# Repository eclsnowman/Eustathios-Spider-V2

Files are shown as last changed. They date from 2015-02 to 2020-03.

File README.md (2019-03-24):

# Eustathios Spider - V2
Update to Eustathios with a little bit of HercuLien design changes.

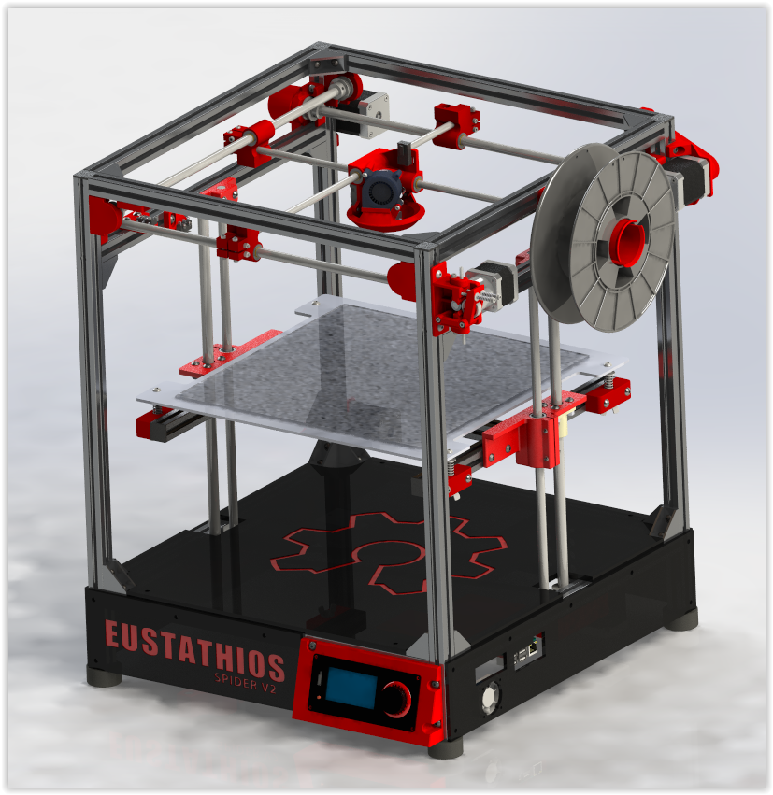
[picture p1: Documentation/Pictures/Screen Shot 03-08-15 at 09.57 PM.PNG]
Eustathios Spider - V2 Render Image


Hello and welcome to my github for Eustathios Spider V2 3D printer. This printer is my attempt to make additional modifications and improvements to the original Eustathios Spider design I published earlier. This has been no small task since the Eustathios printer (designed by Jason Smith) was such an exceptional design to begin with. Now that Google+ has died, the Community around the HercuLien printer and the Eustathios printer have moved to: https://forum.makerforums.info/c/herculien . This is thanks in great part to Michael K Johnson, who worked his magic to retain the years of great community interaction on G+ and ported it into the Discourse community over on Makerforums. If you are looking for support or community interaction on these printers moving forward, this is the place to go.

This family of printers is all based on the X/Y gantry mechanics of the Ultimaker. Ultimaker style mechanics utilizes a light hot-end/carriage which gets constrained by one X and one Y cross rod. Connected to these cross rods are rod ends which ride on side shafts that act both for power transmission of one axis (rotation) and as the linear guide for travel of the other axis (translation).

 Originally a gentlemen who goes by the name Sublime (https://github.com/Intrinsically-Sublime/Tantillus/) created a small format variant of the Ultimaker mechanics which he called the Tantillus. Then GoopyPlastic (aka Brad Hill) created an extrusion version of the Tantillus called the tslot Tantillus (https://github.com/goopyplastic/tslot-tantillus). Following in Brad’s footsteps Tim Rastall (https://plus.google.com/u/0/+TimRastall/posts) created the very popular Ingentis printer (https://www.youmagine.com/designs/ingentis-a-tantillus-variant) which is a larger version of Tantilus using thicker linear guide components, spectra drive system, and a much larger build envelope. The next printer in this design family was by Jason Smith (https://plus.google.com/u/0/103009815307828556107/posts) call the Eustathios (https://github.com/jasonsmit4/Eustathios). This is the printer that got me excited about this family of printers. Jason made several design choices like GT2 belts which I felt were great upgrades to the platform. I lucked out because his release was timed perfectly with a promotion Misumi was running where your first order from them up to $150 in value was free. I wanted to be able to modify Jason’s files slightly, but he had modeled everything in Sketchup. My limited experience was with Solidworks (self taught) so rather than learn new software I redrew Jason’s Eustathios design files from scratch. And so my Eustathios Spider V1 variant , named due to the color scheme, was born (https://github.com/eclsnowman/Lien3D_Eustathios_Spider). I built the Eustathios and fell in love with the smooth operation, clean prints, and overall reliability. So after operating the Eustathios for several months I converted my existing large CoreXY Printer (https://github.com/eclsnowman/Lien3D_CoreXY ) into a X/Y gantry printer with larger cross rods and dual extrusion. The name of this printer is HercuLien (https://github.com/eclsnowman/HercuLien).

Sorry for the long history lesson, but as you can see there is a lot of progress and talented people involved in these projects. Also I wanted to make sure credit is properly attributed to the many great makers who have come before me. The caliber of people involved and all the creativity in the platform is what keeps me so motivated.

Eustathios Spider V2 Overview:

Build Volume: 285x285x295mm

Controler: Azteeg X5 Mini with Viki2 LCD display

Single Extruder, 200W 24V power supply for controls, 120V 500W heated bed through SSR control.

Documentation:

BOM = https://github.com/eclsnowman/Eustathios-Spider-V2/blob/master/Documentation/BOM/Eustathios%20Spider%20V2%20BOM.xlsx

Printable STL Parts = https://github.com/eclsnowman/Eustathios-Spider-V2/tree/master/STL%20Print%20FIles

Solidworks Files = https://github.com/eclsnowman/Eustathios-Spider-V2/tree/master/STL%20Print%20FIles

Other 3D model formats in 7zip due to github 50mb limit) = https://github.com/eclsnowman/Eustathios-Spider-V2/tree/master/Other%203D%20Formats

3D renders: https://github.com/eclsnowman/Eustathios-Spider-V2/tree/master/Documentation/Pictures

Image of printed parts:
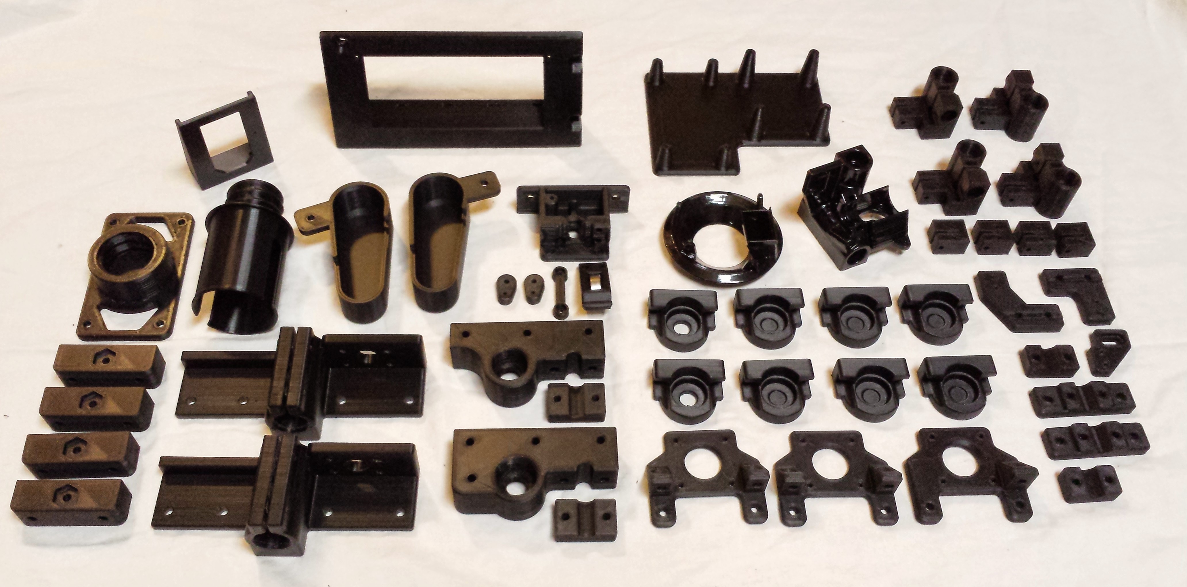
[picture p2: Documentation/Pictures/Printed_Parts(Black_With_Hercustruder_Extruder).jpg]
Eustathios Spider - V2 Printed Parts Image


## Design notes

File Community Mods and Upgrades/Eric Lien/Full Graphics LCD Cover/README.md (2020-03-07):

Note this works for the V1.5 Frame, but not yet for the V2 frame due to the lower frame crossbars. I am working on updating it for the V2 frame.

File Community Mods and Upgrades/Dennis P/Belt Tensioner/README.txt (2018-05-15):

Remix of Walter Hsiao's 8mm Belt tensioner. Changes include bores for brass thread heatserts for the M5 and M3 screws. 

Left and Right delimiter is arbitrary- its only used to describe the 2 mirror images. 

Required fasteners are: 
M5x25 for the 8mm rod clamp 
M3x30 for the belt tensioner

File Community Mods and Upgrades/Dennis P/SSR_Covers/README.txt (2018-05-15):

The knockoff uxcell SSR-10DA 10A DC 3-32V to AC 24V-380V SSR Solid State I used did not have terminal protectors on either the high or low voltage terminals. 

These covers were designed for M4 fixing screws to be utilized with hammer nuts in your extrusion or to the provided heatsink.

The 3mm LED hole is for a pre-wired 12V indicator LED to be used on the 12V side, wired in parallel to the heatbed trigger circuit so that you may be able to visually verify that the SSR is being triggered by the controller board.

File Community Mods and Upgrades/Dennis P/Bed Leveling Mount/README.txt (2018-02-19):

Bed Levelling Mount Remix by D. Pantazis

1. Bed levelling blocks reconfigured with annotations for adjusting the nozzle / bed gap. 

2. Graduated thumb wheel to aid in adjusting the bed. 

3. Test flat of the recessed test to tweak printer settings. 

4. Spring keeper centering washer for top of spring. To center and align the spring to the M5 stud/nut. 

Blocks attach to 20x20 frame with M5x20 cap head screws. 

Levelling studs for bed attachment M5x60 double nutted to heat spreader plate.  

Springs are 1/2" OD x 1" min length.

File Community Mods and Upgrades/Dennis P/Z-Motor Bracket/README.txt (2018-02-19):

Alternate Z motor mount bracket- I goofed when I ordered belts and ordered one too short.
 
I decided to make use of an additional crossbar and put the tensioner on a revised Z motor mount. 

Z Motor rotated 45 degrees to get the tensioner closer to the spindle to get better belt wrap on the idler and motor pulley.

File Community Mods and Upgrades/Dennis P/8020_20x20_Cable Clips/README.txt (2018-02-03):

8020 profiles are a little different than some of the other ones, notably the channel is 5.25mm wide. 

These cable clips are designed to twist in through the slots. 

If you print with a brim, leave the brim on the toggle and stud, it will act as a spring to keep the clip snugly in place.

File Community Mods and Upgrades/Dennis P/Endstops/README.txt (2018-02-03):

Makerbot style endstop switch holders for X, Y & Z axis. 

Included are holders for both MAX & MIN locations, though only the MIN's are normally required. 

Reliefs in the parts for the solder buildup and header pins may required some adjustment and opening up for the PCB's to sit flat. YMMV....

The thru fixing holes in brackets are 2.5mm for making threads with an M3 spiral point tap so that the chips eject out the back of the part.

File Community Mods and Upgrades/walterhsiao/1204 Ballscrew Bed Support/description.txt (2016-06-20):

Replacement for Z_Axis_Bed_Support, designed to be compatible to 1204 ballscrews instead of the 12mm lead screws.  More info at http://www.thingiverse.com/thing:854267

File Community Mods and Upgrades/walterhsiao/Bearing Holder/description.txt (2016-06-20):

Alternate bearing holder design.  More info at http://www.thingiverse.com/thing:854360

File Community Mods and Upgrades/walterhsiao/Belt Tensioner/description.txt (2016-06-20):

Alternate belt tensioner design, designed to be used with graphite bushings and supports slightly longer cross rods.  Versions are available for 8mm and 10mm cross rods.  More info at http://www.thingiverse.com/thing:854301

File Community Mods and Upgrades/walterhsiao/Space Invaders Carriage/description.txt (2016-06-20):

Alternate E3Dv6 carriage design.  Nozzle height is significantly higher than the original carriage and my not be compatible without other changes.  More info at http://www.thingiverse.com/thing:1322641.

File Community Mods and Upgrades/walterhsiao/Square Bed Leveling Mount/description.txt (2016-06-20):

Replacement for Bed_Leveling_Mount, designed to be used with a rectangular heated bed.  More info at http://www.thingiverse.com/thing:854260

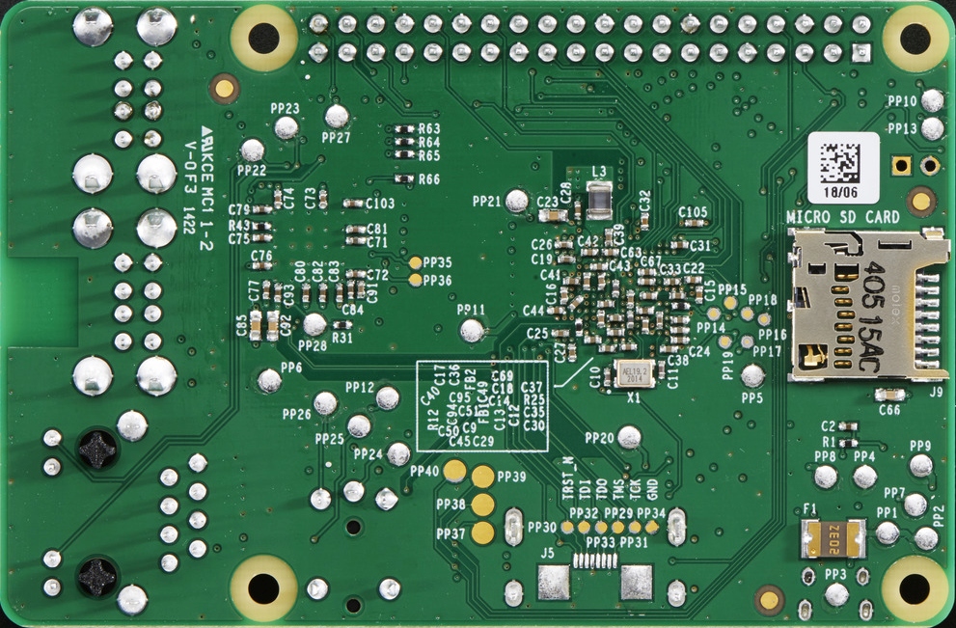
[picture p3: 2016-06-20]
Solidworks/Electronics/Amazon/Raspberry Pi/@raspberry_pi_model_B+_bot_2.jpg

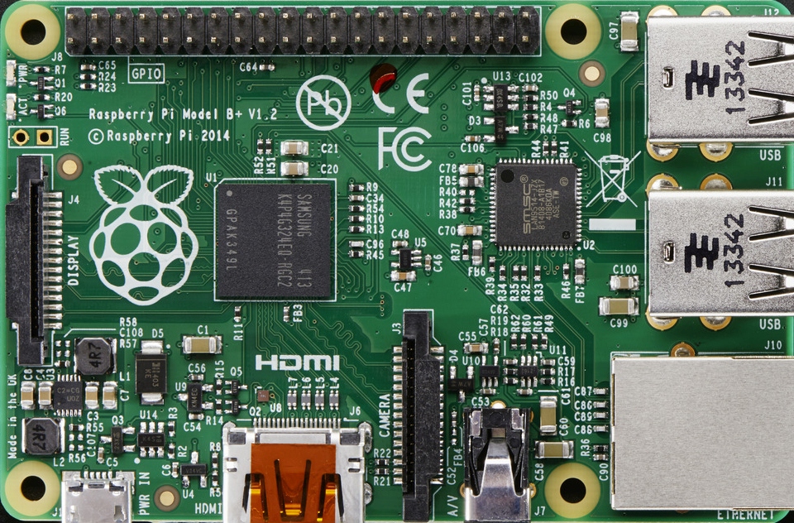
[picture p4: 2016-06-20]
Solidworks/Electronics/Amazon/Raspberry Pi/@raspberry_pi_model_B+_top_1.jpg

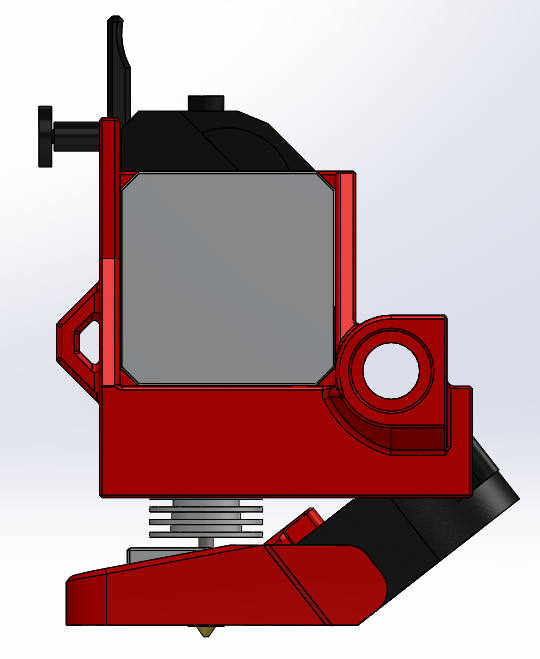
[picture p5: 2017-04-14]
Community Mods and Upgrades/Eric Lien/Eustathios BMG Carriage/Pictures/Screen Shot 04-14-17 at 12.22 PM 002.PNG

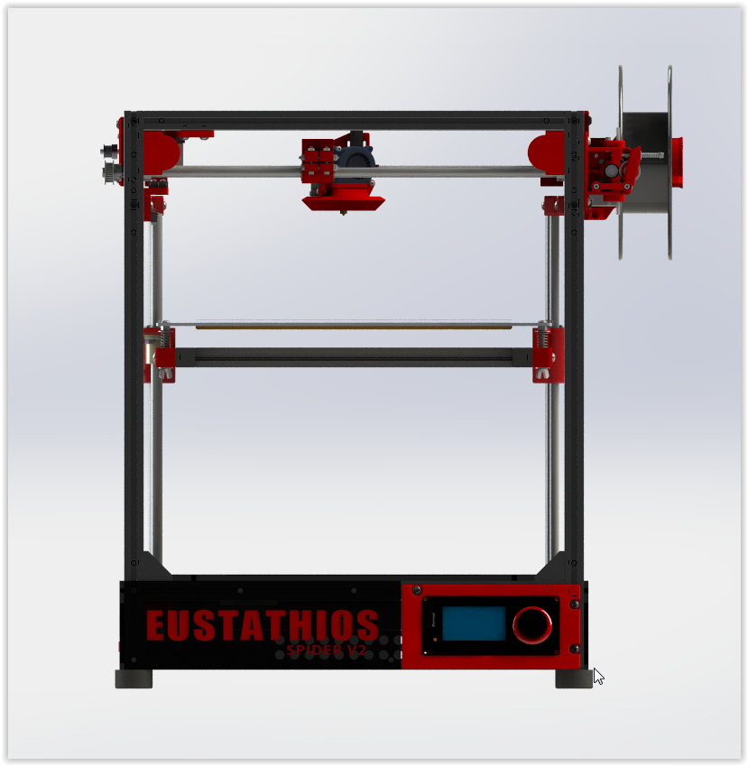
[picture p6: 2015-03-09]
Documentation/Pictures/Screen Shot 03-08-15 at 04.17 PM.PNG

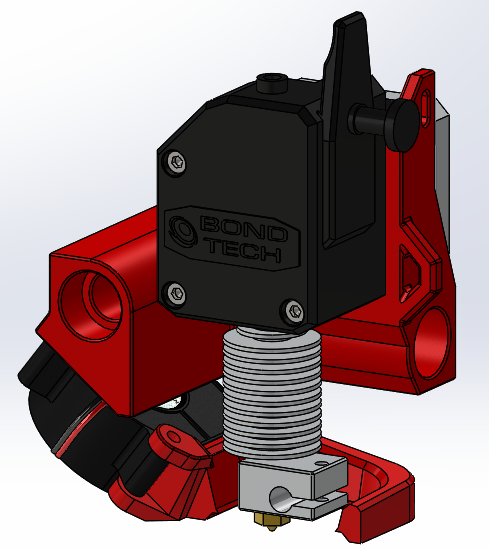
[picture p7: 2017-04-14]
Community Mods and Upgrades/Eric Lien/Eustathios BMG Carriage/Pictures/Screen Shot 04-14-17 at 12.23 PM.PNG

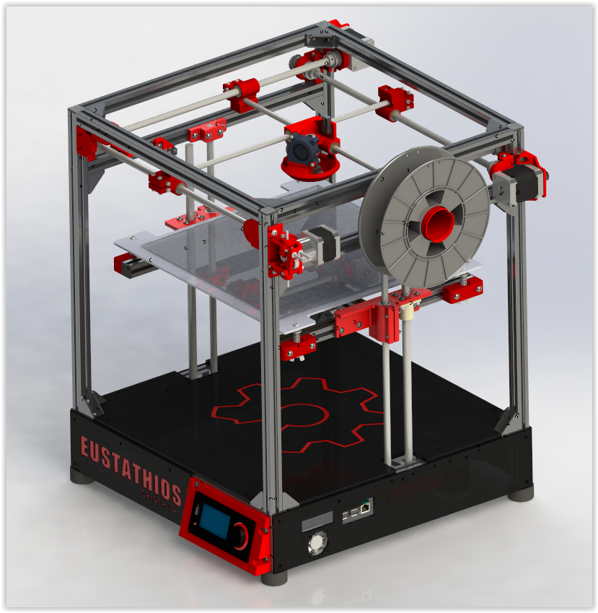
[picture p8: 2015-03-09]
Documentation/Pictures/Screen Shot 03-08-15 at 04.13 PM.PNG

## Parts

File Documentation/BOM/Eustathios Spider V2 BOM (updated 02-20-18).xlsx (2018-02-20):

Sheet: SUBASSY
SUBASSY # | ITEM NO. | PART NUMBER | DESCRIPTION | Vendor | Qty of SUBASSY | Qty per SUBASSY | Total Per SUBASSY
1 |  | Eustathios_Frame |  |  | 1
 | 1.1 | HFSB5-2020-562-LTP-RCP-FR-AH470-AP80 | 20x20x562mm Extruded Aluminum W/ Holes | Misumi or SMW3D |  | 4 | 4
 | 1.2 | HFSB5-2020-425-TPW | 20x20x425mm Extruded Aluminum W/ Tapped Ends | Misumi or SMW3D |  | 10 | 10
 | 1.3 | 91239A224 | 5mm x 10mm button head screw (100 Pack) | McMaster |  | 20 | 20
 | 1.4 | HFC5-2020-B | Black Extrusion Endcap | Misumi |  | 4 | 4
 | 1.5 | HBLFSNB5_W_Hardware | Corner Bracket Subassy | NA (Subassembly) | 16
 | 1.5.1 | HBLFSNB5 | 5 Series, Reversal Brackets with Tab | Misumi |  | 1 | 16
 | 1.5.2 | HNTTSN5-5 | T-Slot Nuts | Misumi or SMW3D |  | 2 | 32
 | 1.5.3 | 91239A224 | 5mm x 10mm button head screw | McMaster |  | 2 | 32
 | 1.6 | 9540K28 | 1.5inX.75inX.25inHole_Foot (10 Pack) | McMaster |  | 4 | 4
 | 1.7 | 91239A232 | 5mm x 16mm button head socket cap screw | McMaster |  | 4 | 4
 | 1.8 | Jamicon_KF0410-01 | 40x40mm 24v fan | Ultimachine |  | 1 | 1
 | 1.9 | Acrylic_or_Polycarbonate_Bottom_Plate | Fabricated - .177in thick Acrylic or Polycarbonate | Amazon |  | 1 | 1
 | 1.10 | Acrylic_or_Polycarbonate_Right_Bottom | Fabricated - .177in thick Acrylic or Polycarbonate | Amazon |  | 1 | 1
 | 1.11 | Acrylic_or_Polycarbonate_Back_Bottom | Fabricated - .177in thick Acrylic or Polycarbonate | Amazon |  | 1 | 1
 | 1.12 | Acrylic_or_Polycarbonate_Left_Bottom | Fabricated - .177in thick Acrylic or Polycarbonate | Amazon |  | 1 | 1
 | 1.13 | Acrylic_or_Polycarbonate_Front_Bottom | Fabricated - .177in thick Acrylic or Polycarbonate | Amazon |  | 1 | 1
2 |  | XY_Axis_A |  |  | 1
 | 2.1 | SFJ10-458 | 10mm OD x 458mm Long Precision Linear Shaft | Misumi or SMW3D |  | 1 | 1
 | 2.2 | 10mm_Rod_End_Bearing_Assembly | End Bearing Subassy | NA (Subassembly) | 2
 | 2.2.1 | Bearing_Holder | 3D Printed | 3D Printed |  | 1 | 2
 | 2.2.2 | 5972K164 | 10mm x 22mm x 6mm (6900 series bearing) | Robotdigg |  | 1 | 2
 | 2.2.3 | 92095A210 | 5mm x 12mm button head socket cap screw | McMaster |  | 2 | 4
 | 2.2.4 | HNTTSN5-5 | T-Slot Nuts | Misumi or SMW3D |  | 2 | 4
 | 2.2.5 | GT2_Aluminum_Timing_Pulley_32_Tooth | GT2 2mm pitch, 10mm ID, 32 tooth pulley | Robotdigg |  | 1 | 2
 | 2.2.6 | 90214A422 | 10mmx16mmx0.5mm_SHim | McMaster |  | 1 | 2
 | 2.3 | XY_Axis_Belt_Tensioner_A | Rod End With Tensioner (Type A) Subassy | NA (Subassembly) | 1
 | 2.3.1 | XY Axis Belt Tensioner A | 3D Printed | 3D Printed |  | 1 | 1
 | 2.3.2 | a_7z41mpsb10m | 10mm self aligning bronze sintered bushings | Ultibots or SDP/SI or Spyraflo or McMaster |  | 2 | 2
 | 2.3.3 | XY Axis Belt Tensioner End | 3D Printed | 3D Printed |  | 1 | 1
 | 2.3.4 | 91290A125 | 3mm x 25mm socket head cap screw | McMaster |  | 2 | 2
 | 2.3.5 | 90591A121 | 3mm hex nut (Din 934) | McMaster |  | 2 | 2
 | 2.3.6 | 91239A232 | 5mm x 16mm button head socket cap screw | McMaster |  | 1 | 1
 | 2.3.7 | 90591A146 | 3mm standard hex nut (DIN 934) | McMaster |  | 1 | 1
 | 2.3.8 | 90576A102 | 3mm nylock hex nut | McMaster |  | 2 | 2
 | 2.3.9 | 91290A135 | 3mm x 35mm socket head cap screw | McMaster |  | 2 | 2
3 |  | XY_Axis_A (Driven Version/Configuration) |  |  | 1
 | 3.1 | 10mm_Rod_End_Bearing_Assembly (Passthrough) | End Bearing Subassy (Passthrough) | NA (Subassembly) | 1
 | 3.1.1 | Passthrough_Bearing_Holder | 3D Printed | 3D Printed |  | 1 | 1
 | 3.1.2 | 5972K164 | 10mm x 22mm x 6mm (6900 series bearing) | Fasteddy Bearings |  | 1 | 1
 | 3.1.3 | 92095A210 | 5mm x 12mm button head socket cap screw | McMaster |  | 2 | 2
 | 3.1.4 | HNTTSN5-5 | T-Slot Nuts | Misumi or SMW3D |  | 2 | 2
 | 3.1.5 | GT2_Aluminum_Timing_Pulley_32_Tooth | GT2 2mm pitch, 10mm ID, 32 tooth pulley | Robotdigg |  | 1 | 1
 | 3.1.6 | 90214A422 | 10mmx16mmx0.5mm_SHim | McMaster |  | 1 | 1
 | 3.2 | 10mm_Rod_End_Bearing_Assembly | End Bearing Subassy | NA (Subassembly) | 1
 | 3.2.1 | Bearing_Holder | 3D Printed | 3D Printed |  | 1 | 1
 | 3.2.2 | 5972K164 | 10mm x 22mm x 6mm (6900 series bearing) | Fasteddy Bearings |  | 1 | 1
 | 3.2.3 | 92095A210 | 5mm x 12mm button head socket cap screw | McMaster |  | 2 | 2
 | 3.2.4 | HNTTSN5-5 | T-Slot Nuts | Misumi or SMW3D |  | 2 | 2
 | 3.2.5 | GT2_Aluminum_Timing_Pulley_32_Tooth | GT2 2mm pitch, 10mm ID, 32 tooth pulley | Robotdigg |  | 1 | 1
 | 3.2.6 | 90214A422 | 10mmx16mmx0.5mm_SHim | McMaster |  | 1 | 1
 | 3.3 | XY_Axis_Belt_Tensioner_A | Rod End With Tensioner (Type A) Subassy | NA (Subassembly) | 1
 | 3.3.1 | XY Axis Belt Tensioner A | 3D Printed | 3D Printed |  | 1 | 1
 | 3.3.2 | a_7z41mpsb10m | 10mm self aligning bronze sintered bushings | Ultibots or SDP/SI or Spyraflo or McMaster |  | 2 | 2
 | 3.3.3 | XY Axis Belt Tensioner End | 3D Printed | 3D Printed |  | 1 | 1
 | 3.3.4 | 91290A125 | 3mm x 25mm socket head cap screw | McMaster |  | 2 | 2
 | 3.3.5 | 90591A121 | 3mm hex nut (Din 934) | McMaster |  | 2 | 2
 | 3.3.6 | 91239A232 | 5mm x 16mm button head socket cap screw | McMaster |  | 1 | 1
 | 3.3.7 | 90591A146 | 3mm standard hex nut (DIN 934) | McMaster |  | 1 | 1
 | 3.3.8 | 90576A102 | 3mm nylock hex nut | McMaster |  | 2 | 2
 | 3.3.9 | 91290A135 | 3mm x 35mm socket head cap screw | McMaster |  | 2 | 2
 | 3.4 | SFJ10-483 | 10mm OD x 483mm Long Precision Linear Shaft | Misumi or SMW3D |  | 1 | 1
 | 3.5 | GT2_Aluminum_Timing_Pulley_32_Tooth | GT2 2mm pitch, 10mm ID, 32 tooth pulley | Robotdigg |  | 1 | 1
4 |  | XY_Axis_B |  |  | 1
 | 4.1 | SFJ10-458 | 10mm OD x 458mm Long Precision Linear Shaft | Misumi or SMW3D |  | 1 | 1
 | 4.2 | 10mm_Rod_End_Bearing_Assembly | End Bearing Subassy | NA (Subassembly) | 2
 | 4.2.1 | Bearing_Holder | 3D Printed | 3D Printed |  | 1 | 2
 | 4.2.2 | 5972K164 | 10mm x 22mm x 6mm (6900 series bearing) | Fasteddy Bearings |  | 1 | 2
 | 4.2.3 | 92095A210 | 5mm x 12mm button head socket cap screw | McMaster |  | 2 | 4
 | 4.2.4 | HNTTSN5-5 | T-Slot Nuts | Misumi or SMW3D |  | 2 | 4
 | 4.2.5 | GT2_Aluminum_Timing_Pulley_32_Tooth | GT2 2mm pitch, 10mm ID, 32 tooth pulley | Robotdigg |  | 1 | 2
 | 4.2.6 | 90214A422 | 10mmx16mmx0.5mm_SHim | McMaster |  | 1 | 2
 | 4.3 | XY_Axis_Belt_Tensioner_B | Rod End With Tensioner (Type B) Subassy | NA (Subassembly) | 1
 | 4.3.1 | XY Axis Belt Tensioner B | 3D Printed | 3D Printed |  | 1 | 1
 | 4.3.2 | a_7z41mpsb10m | 10mm self aligning bronze sintered bushings | Ultibots or SDP/SI or Spyraflo or McMaster |  | 2 | 2
 | 4.3.3 | XY Axis Belt Tensioner End | 3D Printed | 3D Printed |  | 1 | 1
 | 4.3.4 | 91290A135 | 3mm x 35mm socket head cap screw | McMaster |  | 2 | 2
 | 4.3.5 | 90576A102 | 3mm nylock hex nut | McMaster |  | 4 | 4
 | 4.3.6 | 91239A126 | 3mm x 25mm button head socket cap screw | McMaster |  | 2 | 2
 | 4.3.7 | 90591A146 | 3mm standard hex nut (DIN 934) | McMaster |  | 1 | 1
 | 4.3.8 | 91239A232 | 5mm x 16mm button head socket cap screw | McMaster |  | 1 | 1
5 |  | XY_Axis_B (Driven Version/Configuration) |  |  | 1
 | 5.1 | 10mm_Rod_End_Bearing_Assembly (Passthrough) | End Bearing Subassy (Passthrough) | NA (Subassembly) | 1
 | 5.1.1 | Passthrough_Bearing_Holder | 3D Printed | 3D Printed |  | 1 | 1
 | 5.1.2 | 5972K164 | 10mm x 22mm x 6mm (6900 series bearing) | Fasteddy Bearings |  | 1 | 1
 | 5.1.3 | 92095A210 | 5mm x 12mm button head socket cap screw | McMaster |  | 2 | 2
 | 5.1.4 | HNTTSN5-5 | T-Slot Nuts | Misumi or SMW3D |  | 2 | 2
 | 5.1.5 | GT2_Aluminum_Timing_Pulley_32_Tooth | GT2 2mm pitch, 10mm ID, 32 tooth pulley | Robotdigg |  | 1 | 1
 | 5.1.6 | 90214A422 | 10mmx16mmx0.5mm_SHim | McMaster |  | 1 | 1
 | 5.2 | 10mm_Rod_End_Bearing_Assembly | End Bearing Subassy | NA (Subassembly) | 1
 | 5.2.1 | Bearing_Holder | 3D Printed | 3D Printed |  | 1 | 1
 | 5.2.2 | 5972K164 | 10mm x 22mm x 6mm (6900 series bearing) | Fasteddy Bearings |  | 1 | 1
 | 5.2.3 | 92095A210 | 5mm x 12mm button head socket cap screw | McMaster |  | 2 | 2
 | 5.2.4 | HNTTSN5-5 | T-Slot Nuts | Misumi or SMW3D |  | 2 | 2
 | 5.2.5 | GT2_Aluminum_Timing_Pulley_32_Tooth | GT2 2mm pitch, 10mm ID, 32 tooth pulley | Robotdigg |  | 1 | 1
 | 5.2.6 | 90214A422 | 10mmx16mmx0.5mm_SHim | McMaster |  | 1 | 1
 | 5.3 | XY_Axis_Belt_Tensioner_B | Rod End With Tensioner (Type B) Subassy | NA (Subassembly) | 1
 | 5.3.1 | XY Axis Belt Tensioner B | 3D Printed | 3D Printed |  | 1 | 1
 | 5.3.2 | a_7z41mpsb10m | 10mm self aligning bronze sintered bushings | Ultibots or SDP/SI or Spyraflo or McMaster |  | 2 | 2
 | 5.3.3 | XY Axis Belt Tensioner End | 3D Printed | 3D Printed |  | 1 | 1
 | 5.3.4 | 91290A135 | 3mm x 35mm socket head cap screw | McMaster |  | 2 | 2
 | 5.3.5 | 90576A102 | 3mm nylock hex nut | McMaster |  | 4 | 4
 | 5.3.6 | 91239A126 | 3mm x 25mm button head socket cap screw | McMaster |  | 2 | 2
 | 5.3.7 | 90591A146 | 3mm standard hex nut (DIN 934) | McMaster |  | 1 | 1
 | 5.3.8 | 91239A232 | 5mm x 16mm button head socket cap screw | McMaster |  | 1 | 1
 | 5.4 | SFJ10-483 | 10mm OD x 483mm Long Precision Linear Shaft | Misumi or SMW3D |  | 1 | 1
 | 5.5 | GT2_Aluminum_Timing_Pulley_32_Tooth | GT2 2mm pitch, 10mm ID, 32 tooth pulley | Robotdigg |  | 1 | 1
6 |  | Y_Axis_Endstop |  |  | 1
 | 6.1 | Y Endstop Mount | 3D Printed | 3D Printed |  | 1 | 1
 | 6.2 | Micro Switch Button | NO / NC Limit Switch | Robotdigg or SMW3D |  | 1 | 1
 | 6.3 | HNTTSN5-5 | T-Slot Nuts | Misumi or SMW3D |  | 2 | 2
 | 6.4 | 92095A210 | 5mm x 12mm button head socket cap screw | McMaster |  | 2 | 2
 | 6.5 | 92095A183 | 3mm x 12mm button head socket cap screw | McMaster |  | 2 | 2
7 |  | X_Axis_Endstop |  |  | 1
 | 7.1 | X Endstop Mount | 3D Printed | 3D Printed |  | 1 | 1
 | 7.2 | Micro Switch Button | NO / NC Limit Switch | Robotdigg or SMW3D |  | 1 | 1
 | 7.3 | HNTTSN5-5 | T-Slot Nuts | Misumi or SMW3D |  | 2 | 2
 | 7.4 | 92095A210 | 5mm x 12mm button head socket cap screw | McMaster |  | 2 | 2
 | 7.5 | 92095A183 | 3mm x 12mm button head socket cap screw | McMaster |  | 2 | 2
8 | 8.1 | SFJ8-400 | 8mm OD x 400mm Long Precision Linear Shaft | Misumi or SMW3D |  |  | 2
9 |  | Eustathios_Carriage_V4_Molex_Microfit_3 |  |  | 1
 | 9.1 | Carriage_V4_Molex_Microfit_3 | 3D Printed | 3D Printed |  | 1 | 1
 | 9.2 | 4020Blower | 4020 part cooling blower fan | Ebay |  | 1 | 1
 | 9.3 | E3D_V6 | Hot End (need 24V fan and heater cartridge if 24V power supply is used, by default E3D V6 is designed for 12V system) | E3D or SMW3D |  | 1 | 1
 | 9.4 | 30x30_Fan | included with e3d kit (needs to be 24v if 24V power supply is used) | See Above |  | 1 | 1
 | 9.5 | Carriage_V4_Part_Cooling_Duct | 3D Printed | 3D Printed |  | 1 | 1
 | 9.6 | a_7z41mpsb08m | 8mm self aligning bronze sintered bushings | Ultibots or SDP/SI or Spyraflo or McMaster |  | 4 | 4
 | 9.7 | Molex_430200801 | Molex 430200801 Subassy | NA (Subassembly) | 1
 | 9.7.1 | 430200801 | Conn Plug 8Pos 3mm Vert Dual | Digikey or Moser |  | 1 | 1
 | 9.7.2 | 430310007 | Conn Term Male 20-24AWG Tin | Digikey or Moser |  | 1 | 1
 | 9.8 | Molex_430250800 | Molex 430250800 Subassy | NA (Subassembly) | 1
 | 9.8.1 | 430250800 | Conn Recept 8pos 3mm Vert Dual | Digikey or Moser |  | 1 | 1
 | 9.8.2 | 430300007 | Conn Term Female 20-24AWG Tin | Digikey or Moser |  | 1 | 1
 | 9.9 | 91239A126 | 3mm x 25mm button head socket cap screw | McMaster |  | 1 | 0
 | 9.10 | 92095A185 | 3mm x 20mm button head socket cap screw | McMaster |  | 1 | 1
 | 9.11 | 90591A121 | 3mm hex nut (Din 934) | McMaster |  | 1 | 1
 | 9.12 | 94500A222 | 3mm x 8mm button head socket cap screw | McMaster |  | 3 | 3
 | 9.13 | 92095A184 | 3mm x 16mm button head socket cap screw | McMaster |  | 4 | 4
10 |  | Z_Axis_And_Bed |  |  | 1
 | 10.1 | HFSB5-2020-321-TPW | 20x20x321mm Extruded Aluminum W/ Tapped Ends | Misumi or SMW3D |  | 1 | 1
 | 10.2 | HFSB5-2020-355-AH177_5 | 20x20x355mm Extruded Aluminum W/ Holes | Misumi or SMW3D |  | 2 | 2
 | 10.3 | Z_Axis_Bed_Support | Z Axis Bed Support Subassy | NA (Subassembly) | 2
 | 10.3.1 | Z_Axis_Bed_Support | 3D Printed | 3D Printed |  | 1 | 2
 | 10.3.2 | MTSGR12 | 12mm x 2mm pitch compact flange lead screw nut | Misumi |  | 1 | 2
 | 10.3.3 | LM10LUU | 10mm ID (19mm OD x 55mm) Precision Linear Bearing | Robotdigg |  | 1 | 2
 | 10.3.4 | 91239A232 | 5mm x 16mm button head socket cap screw | McMaster |  | 4 | 8
 | 10.3.5 | 91239A224 | 5mm x 10mm button head screw | McMaster |  | 4 | 8
 | 10.3.6 | 91290A125 | 3mm x 25mm socket head cap screw | McMaster |  | 2 | 4
 | 10.3.7 | 90576A102 | 3mm nylock hex nut | McMaster |  | 2 | 4
 | 10.3.8 | 94205A240 | 5mm nylock nut (DIN 985) | McMaster |  | 4 | 8
 | 10.3.9 | HNTTSN5-5 | T-Slot Nuts | Misumi or SMW3D |  | 4 | 8
 | 10.4 | HFC5-2020-B | Black Extrusion Endcap | Misumi |  | 4 | 4
 | 10.5 | Bed_Leveling_Mount | Bed Leveling Mount Subassy | NA (Subassembly) | 4
 | 10.5.1 | Bed_Leveling_Mount | 3D Printed | 3D Printed |  | 1 | 4
 | 10.5.2 | 91239A232 | 5mm x 16mm button head socket cap screw | McMaster |  | 2 | 8
 | 10.5.3 | HNTTSN5-5 | T-Slot Nuts | Misumi or SMW3D |  | 2 | 8
 | 10.5.4 | 9657K313 | 1Long .5OD 0.062Wire Compression Spring | McMaster |  | 1 | 4
 | 10.5.5 | 92095A483 | 5mm x 55mm button head socket cap screw | McMaster |  | 1 | 4
 | 10.5.6 | 94545A225 | 5mm wing nut (DIN 315) | McMaster |  | 1 | 4
 | 10.5.7 | 94205A240 | 5mm nylock nut (DIN 985) | McMaster |  | 1 | 4
 | 10.5.8 | 91100A140 | 5mm oversized flat washer (DIN 9021) | McMaster |  | 2 | 8
 | 10.6 | Aluminum Heat Spreader Build Plate | 400x360mm (1/8") 5052 Aluminum Plate per DXF | DiscountSteel.com |  | 1 | 1
 | 10.7 | 91239A224 | 5mm x 10mm button head screw | McMaster |  | 2 | 2
 | 10.8 | 320x320_120V_500W_Heated_Bed | 320x320mm/120V/500W Silicon Heated Mat | Alirubber (Aliexpress) |  | 1 | 1
 | 10.9 | 360x345_Glass_Print_Surface | 360x345mm glass print surface (window or boro) | Voxel Factory Or Hardware Store |  | 1 | 1
 | 10.10 | Z_Rod_And_Mounts | Z Rod And Mounts Subassy | NA (Subassembly) | 2
 | 10.10.1 | SFJ10-435 | 10mm OD x 435mm Long Precision Linear Shaft | Misumi or SMW3D |  | 1 | 2
 | 10.10.2 | Z_Axis_Shaft_Mount_A | 3D Printed | 3D Printed |  | 1 | 2
 | 10.10.3 | Z_Axis_Shaft_Mount_B | 3D Printed | 3D Printed |  | 1 | 2
 | 10.10.4 | 94205A240 | 5mm nylock nut (DIN 985) | McMaster |  | 2 | 4
 | 10.10.5 | 91239A232 | 5mm x 16mm button head socket cap screw | McMaster |  | 2 | 4
 | 10.10.6 | 92095A210 | 5mm x 12mm button head socket cap screw | McMaster |  | 2 | 4
 | 10.10.7 | HNTTSN5-5 | T-Slot Nuts | Misumi or SMW3D |  | 2 | 4
 | 10.11 | Z-Screw_Support_V2 | Z-Screw Support Subassy | NA (Subassembly) | 1
 | 10.11.1 | Z_Axis_Leadscrew_Support_V2 | 3D Printed | 3D Printed |  | 1 | 1
 | 10.11.2 | 6082Z-8x22x7 | 608 skate bearing | Robotdigg or SMW3D |  | 2 | 2
 | 10.11.3 | 90214A418 | 8mm ID Thin Bearing Shim | McMaster |  | 1 | 1
 | 10.11.4 | GT2_Aluminum_Timing_Pulley_32_Tooth_8mm | GT2 2mm pitch, 8mm ID, 32 tooth pulley | Robotdigg |  | 1 | 1
 | 10.11.5 | 91290A252 | 5mm x 25mm socket head cap screw | McMaster |  | 5 | 5
 | 10.11.6 | HNTTSN5-5 | T-Slot Nuts | Misumi or SMW3D |  | 3 | 3
 | 10.11.7 | MTSBRB12-425-S46-Q8-C3-J0 | 12mm x 2mm pitch Lead Screw, 46mm Long x 8mm OD Step | Misumi (Instead Get Ballscrew from Goalmart) |  | 1 | 1
 | 10.11.8 | 57485K67 | 8mm ID Set Screw Shaft Collar | McMaster |  | 1 | 1
 | 10.11.9 | Z_Axis_Leadscrew_Support_Clamp_V2 | 3D Printed | 3D Printed |  | 1 | 1
 | 10.11.10 | 90591A146 | 3mm standard hex nut (DIN 934) | McMaster |  | 2 | 2
 | 10.12 | Z-Screw_Support_V2 (With Tensioner Config) | Z-Screw Support Subassy (With Tensioner) | NA (Subassembly) | 1
 | 10.12.1 | Z_Axis_Leadscrew_Support_V2 (With Tensioner Config) | 3D Printed | 3D Printed |  | 1 | 1
 | 10.12.2 | 6082Z-8x22x7 | 608 skate bearing | Robotdigg or SMW3D |  | 2 | 2
 | 10.12.3 | 8mm ID Thin Bearing Shim | 8mm ID Thin Bearing Shim | McMaster |  | 1 | 1
 | 10.12.4 | GT2_Aluminum_Timing_Pulley_32_Tooth_8mm | GT2 2mm pitch, 8mm ID, 32 tooth pulley | Robotdigg |  | 1 | 1
 | 10.12.5 | 91290A252 | 5mm x 25mm socket head cap screw | McMaster |  | 5 | 5
 | 10.12.6 | HNTTSN5-5 | T-Slot Nuts | Misumi or SMW3D |  | 3 | 3
 | 10.12.7 | MTSBRB12-425-S46-Q8-C3-J0 | 12mm x 2mm pitch Lead Screw, 46mm Long x 8mm OD Step | Misumi (Instead Get Ballscrew from Goalmart) |  | 1 | 1
 | 10.12.8 | 57485K67 | 8mm ID Set Screw Shaft Collar | McMaster |  | 1 | 1
 | 10.12.9 | Z_Axis_Leadscrew_Support_Clamp_V2 | 3D Printed | 3D Printed |  | 1 | 1
 | 10.12.10 | 90591A146 | 3mm standard hex nut (DIN 934) | McMaster |  | 2 | 2
 | 10.12.11 | Idler Wheel Assembly | Idler Wheel Subassy | NA (Subassembly) | 1
 | 10.12.11.1 | V-Slot Idler Pulley | V-Slot Idler Pulley | SMW3D or Openbuilds |  | 1 | 1
 | 10.12.11.2 | Precision Ball Bearing | Precision Ball Bearing | SMW3D or Openbuilds |  | 2 | 2
 | 10.12.11.3 | 5mm Precision Washer | 5mm Precision Washer | SMW3D or Openbuilds |  | 1 | 1
 | 10.12.11.4 | Nylon Insert Hex Locknut 5mm | Nylon Insert Hex Locknut 5mm | SMW3D or Openbuilds |  | 1 | 1
 | 10.12.11.5 | 92095A220 | 5mm X 35mm button head socket cap screw | McMaster |  | 1 | 1
 | 10.12.11.6 | .125 Inch Aluminum Spacer | .125 Inch Aluminum Spacer | SMW3D or Openbuilds |  | 1 | 1
11 |  | Z Endstop |  |  | 1
 | 11.1 | Z Endstop Mount V2 | 3D Printed | NA (Subassembly) |  | 1 | 1
 | 11.2 | HNTTSN5-5 | T-Slot Nuts | Misumi or SMW3D |  | 1 | 1
 | 11.3 | 92095A183 | 3mm x 12mm button head socket cap screw | McMaster |  | 2 | 2
 | 11.4 | Micro Switch Button | NO / NC Limit Switch | Robotdigg or SMW3D |  | 1 | 1
 | 11.5 | 91239A224 | 5mm x 10mm button head screw | McMaster |  | 1 | 1
12 |  | Motor_Mount_With_Nema17_60mm (For X and Y Drive) |  |  | 2
 | 12.1 | External_Motor | 3D Printed | 3D Printed |  | 1 | 2
 | 12.2 | NEMA_17_60mm_1.5A | 6.5kg/cm 60mm Long Nema 17 Stepper Motor | Robotdigg |  | 1 | 2
 | 12.3 | 94500A223 | 3mm x 10mm button head socket cap screw | McMaster |  | 4 | 8
 | 12.4 | 91239A224 | 5mm x 10mm button head screw | McMaster |  | 4 | 8
 | 12.5 | HNTTSN5-5 | T-Slot Nuts | Misumi or SMW3D |  | 4 | 8
 | 12.6 | GT2_Aluminum_Timing_Pulley_20_Tooth | GT2 2mm pitch, 5mm ID, 20 tooth pulley | Robotdigg or SMW3D |  | 1 | 2
13 |  | Z_Stepper_Module |  |  | 1
 | 13.1 | Z_Stepper_Mount_V2 | 3D Printed | 3D Printed |  | 1 | 1
 | 13.2 | NEMA_17_60mm_1.5A | 6.5kg/cm 60mm Long Nema 17 Stepper Motor | Robotdigg |  | 1 | 1
 | 13.3 | GT2_Aluminum_Timing_Pulley_20_Tooth | GT2 2mm pitch, 5mm ID, 20 tooth pulley | Robotdigg or SMW3D |  | 1 | 1
 | 13.4 | 92095A183 | 3mm x 12mm button head socket cap screw | McMaster |  | 4 | 4
 | 13.5 | 93475A210 | 3mm flat washer (DIN 125) | McMaster |  | 4 | 4
 | 13.6 | 92095A210 | 5mm x 12mm button head socket cap screw | McMaster |  | 2 | 2
 | 13.7 | 91239A224 | 5mm x 10mm button head screw | McMaster |  | 1 | 1
 | 13.8 | HNTTSN5-5 | T-Slot Nuts | Misumi or SMW3D |  | 3 | 3
14 | 14.1 | Meanwell_SP-200-24 | 200W / 24V Power Supply | Allied Electronics or Mouser |  |  | 1
15 | 15.1 | G3N_220B_SSR | Omron Solid State Relay | Amazon |  |  | 1
16 |  | Viki2_LCD_Module |  |  | 1
 | 16.1 | Viki2_Mount | 3D Printed | 3D Printed |  | 1 | 1
 | 16.2 | Viki2_LCD | Panucatt Devices Viki2 LCD Display/Controller | Panucatt Devices |  | 1 | 1
 | 16.3 | 91239A224 | 5mm x 10mm button head screw | McMaster |  | 3 | 3
 | 16.4 | HNTTSN5-5 | T-Slot Nuts | Misumi or SMW3D |  | 3 | 3
17 |  | Belts and Belt Covers |  |  | 1
 | 17.1 | Z Drive Closed Loop Belt (976mm) | GT2 2mm pitch, 6mm wide, 976mm Closed Loop Belt | Robotdigg |  | 1 | 1
 | 17.2 | X/Y Drive Closed Loop Belt (180mm) | GT2 2mm pitch, 6mm wide, 180mm Closed Loop Belt | Robotdigg |  | 2 | 2
 | 17.3 | X/Y Bulk Belt | GT2 2mm pitch, 6mm wide (Per Meter Length) | Robotdigg |  | 4 | 4
 | 17.4 | X_Belt_Guard | 3D Printed | 3D Printed |  | 1 | 1
 | 17.5 | Y_Belt_Guard | 3D Printed | 3D Printed |  | 1 | 1
18 |  | Electronic_Package_V3 |  |  | 1
 | 18.1 | Raspberry Pi 2 | Raspberry Pi 2 | Amazon |  | 1 | 1
 | 18.2 | Azteeg_X5_Mini | Panucatt - Azteeg X5 Mini | Panucatt Devices |  | 1 | 1
 | 18.3 | Electronic_Package Mount | 3D Printed | 3D Printed |  | 1 | 1
19 |  | Outlet_Switch |  |  | 1
 | 19.1 | Outlet_Switch_Mount | 3D Printed | 3D Printed |  | 1 | 1
 | 19.2 | Amazon_Electrical_Fused_Plug | Fused Plug Switch (10A/250V AC/3 Pin IEC320 C14) | Amazon |  | 1 | 1
 | 19.3 | 91239A224 | 5mm x 10mm button head screw | McMaster |  | 2 | 2
 | 19.4 | HNTTSN5-5 | T-Slot Nuts | Misumi or SMW3D |  | 2 | 2
20 |  | HercuStruder_V2 | (recommended alternative = Bondtech Extruder) |  | 1
 | 20.1 | HercuLien_Extruder_Base_V2 | 3D Printed | 3D Printed |  | 1 | 1
 | 20.2 | HercuStruder_Bearing_Pivot | 3D Printed | 3D Printed |  | 1 | 1
 | 20.3 | HercuStruder_Dogbone_Connector | 3D Printed | 3D Printed |  | 1 | 1
 | 20.4 | 6082Z-8x22x7 | 608 skate bearing | Robotdigg or SMW3D |  | 1 | 1
 | 20.5 | 8mm_Shaft_Hobb_Gear | 8mm ID Shaft Hobb Gear | Maker Tool Works or Triad Printing |  | 1 | 1
 | 20.6 | NEMA_17_5.18_Planetary | 40mm Long NEMA 17 Stepper w/ 5.18 Planetary Reduction | Robotdigg |  | 1 | 1
 | 20.7 | HercuStruder_Pin | 3D Printed | 3D Printed |  | 1 | 1
 | 20.8 | Bowden_Tube_Nut_Trap | 3D Printed | 3D Printed |  | 2 | 2
 | 20.9 | 90591A121 | 3mm hex nut (Din 934) | McMaster |  | 4 | 4
 | 20.10 | 91290A137 | 3mm x 50mm socket head cap screw | McMaster |  | 2 | 2
 | 20.11 | 93475A210 | 3mm flat washer (DIN 125) | McMaster |  | 4 | 4
 | 20.12 | 9657K283 | Spring (0.75"L x 0.187" OD x 0.029" Wire) | McMaster |  | 2 | 2
 | 20.13 | 91100A120 | 3mm oversized flat washer (Din 9021) | McMaster |  | 2 | 2
 | 20.14 | 91290A117 |  | McMaster |  | 2 | 2
 | 20.15 | 91239A115 |  | McMaster |  | 4 | 4
 | 20.16 | 91290A135 | 3mm x 35mm socket head cap screw | McMaster |  | 2 | 2
 | 20.17 | 90576A102 | 3mm nylock hex nut | McMaster |  | 2 | 2
 | 20.18 | 91239A224 | 5mm x 10mm button head screw | McMaster |  | 2 | 2
 | 20.19 | HNTTSN5-5 | T-Slot Nuts | Misumi or SMW3D |  | 2 | 2
 | 20.20 | 90545A009 |  | McMaster |  | 2 | 2
 | 20.21 | 4mmODx2mmID_Teflon_Tube | 2mm ID 4mm OD Bowden Tube (10 meters) | Robotdigg |  | 1 | 1
21 |  | Spool_and_Holder |  |  | 1
 | 21.1 | Eustathios_Threaded_Flange | 3D Printed | 3D Printed |  | 1 | 1
 | 21.2 | 50mm_Threaded_Spool_Holder_Full_Round | 3D Printed | 3D Printed |  | 1 | 1
 | 21.3 | Spool | Misc for visual only | NA |  | 1 | 1
 | 21.4 | HNTTSN5-5 | T-Slot Nuts | Misumi or SMW3D |  | 4 | 4
 | 21.5 | 91239A224 | 5mm x 10mm button head screw | McMaster |  | 4 | 4

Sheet: Sum Of Parts Pivot
Parts By Vendor | Qty
3D Printed | 50
50mm_Threaded_Spool_Holder_Full_Round | 1
Bearing_Holder | 6
Bed_Leveling_Mount | 4
Bowden_Tube_Nut_Trap | 2
Carriage_V4_Molex_Microfit_3 | 1
Carriage_V4_Part_Cooling_Duct | 1
Electronic_Package Mount | 1
Eustathios_Threaded_Flange | 1
External_Motor | 2
HercuLien_Extruder_Base_V2 | 1
HercuStruder_Bearing_Pivot | 1
HercuStruder_Dogbone_Connector | 1
HercuStruder_Pin | 1
Outlet_Switch_Mount | 1
Passthrough_Bearing_Holder | 2
Viki2_Mount | 1
X Endstop Mount | 1
X_Belt_Guard | 1
XY Axis Belt Tensioner A | 2
XY Axis Belt Tensioner B | 2
XY Axis Belt Tensioner End | 4
Y Endstop Mount | 1
Y_Belt_Guard | 1
Z_Axis_Bed_Support | 2
Z_Axis_Leadscrew_Support_Clamp_V2 | 2
Z_Axis_Leadscrew_Support_V2 | 1
Z_Axis_Leadscrew_Support_V2 (With Tensioner Config) | 1
Z_Axis_Shaft_Mount_A | 2
Z_Axis_Shaft_Mount_B | 2
Z_Stepper_Mount_V2 | 1
Alirubber (Aliexpress) | 1
320x320_120V_500W_Heated_Bed | 1
Allied Electronics or Mouser | 1
Meanwell_SP-200-24 | 1
Amazon | 8
Acrylic_or_Polycarbonate_Back_Bottom | 1
Acrylic_or_Polycarbonate_Bottom_Plate | 1
Acrylic_or_Polycarbonate_Front_Bottom | 1
Acrylic_or_Polycarbonate_Left_Bottom | 1
Acrylic_or_Polycarbonate_Right_Bottom | 1
Amazon_Electrical_Fused_Plug | 1
G3N_220B_SSR | 1
Raspberry Pi 2 | 1
Digikey or Moser | 4
430200801 | 1
430250800 | 1
430300007 | 1
430310007 | 1
DiscountSteel.com | 1
Aluminum Heat Spreader Build Plate | 1
E3D or SMW3D | 1
E3D_V6 | 1
Ebay | 1
4020Blower | 1
Fasteddy Bearings | 6
5972K164 | 6
Maker Tool Works or Triad Printing | 1
8mm_Shaft_Hobb_Gear | 1
McMaster | 305 | * Note Cheaper harware can be purchased from Trimcraft Aviation RC (Gino over there is awsome)
57485K67 | 2 | https://www.trimcraftaviationrc.com/
8mm ID Thin Bearing Shim | 1 | * Note Most of the quantities below are by the bag/box on mcmaster. To buy from Trimcraft, you need to make sure the lot sizes match up.
90214A418 | 1
90214A422 | 8
90545A009 | 2
90576A102 | 18
90591A121 | 9
90591A146 | 8
91100A120 | 2
91100A140 | 8
91239A115 | 4
91239A126 | 4
91239A224 | 83
91239A232 | 28
91290A117 | 2
91290A125 | 8
91290A135 | 10
91290A137 | 2
91290A252 | 10
92095A183 | 10
92095A184 | 4
92095A185 | 1
92095A210 | 26
92095A220 | 1
92095A483 | 4
93475A210 | 8
94205A240 | 16
94500A222 | 3
94500A223 | 8
94545A225 | 4
9540K28 | 4
9657K283 | 2
9657K313 | 4
Misumi | 26
HBLFSNB5 | 16
HFC5-2020-B | 8
MTSGR12 | 2
Misumi or SMW3D | 126
HFSB5-2020-321-TPW | 1
HFSB5-2020-355-AH177_5 | 2
HFSB5-2020-425-TPW | 10
HFSB5-2020-562-LTP-RCP-FR-AH470-AP80 | 4
HNTTSN5-5 | 101
SFJ10-435 | 2
SFJ10-458 | 2
SFJ10-483 | 2
SFJ8-400 | 2
Panucatt Devices | 2
Azteeg_X5_Mini | 1
Viki2_LCD | 1
Robotdigg | 28
4mmODx2mmID_Teflon_Tube | 1
5972K164 | 2
GT2_Aluminum_Timing_Pulley_32_Tooth | 10
GT2_Aluminum_Timing_Pulley_32_Tooth_8mm | 2
LM10LUU | 2
NEMA_17_5.18_Planetary | 1
NEMA_17_60mm_1.5A | 3
X/Y Bulk Belt | 4
X/Y Drive Closed Loop Belt (180mm) | 2
Z Drive Closed Loop Belt (976mm) | 1
Robotdigg or SMW3D | 11
6082Z-8x22x7 | 5
GT2_Aluminum_Timing_Pulley_20_Tooth | 3
Micro Switch Button | 3
SMW3D or Openbuilds | 6
.125 Inch Aluminum Spacer | 1
5mm Precision Washer | 1
Nylon Insert Hex Locknut 5mm | 1
Precision Ball Bearing | 2
V-Slot Idler Pulley | 1
Ultimachine | 1
Jamicon_KF0410-01 | 1
Voxel Factory Or Hardware Store | 1
360x345_Glass_Print_Surface | 1
Ultibots or SDP/SI or Spyraflo or McMaster | 12
a_7z41mpsb08m | 4
a_7z41mpsb10m | 8
Misumi (Instead Get Ballscrew from Goalmart) | 2
MTSBRB12-425-S46-Q8-C3-J0 | 2 | https://www.aliexpress.com/store/product/Best-quality-1pc-Ball-screw-SFU1204-L425mm-1pc-RM1204-Ballscrew-Ballnut-standard-processing-for-CNC-BK10/920371_32592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
Grand Total | 597

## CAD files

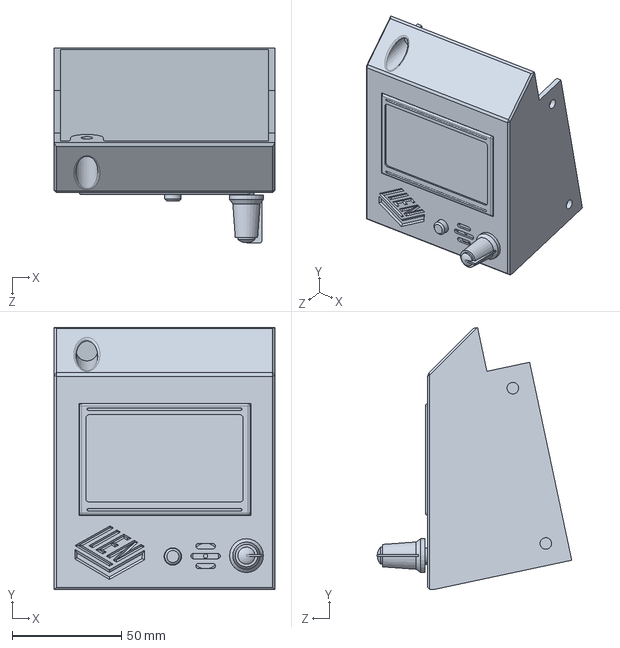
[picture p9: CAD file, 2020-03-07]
Community Mods and Upgrades/Eric Lien/Full Graphics LCD Cover/Eustathios RepRapDiscount_Full Graphic Smart Controller.SLDPRT
101.0 x 119.9 x 89.0 mm

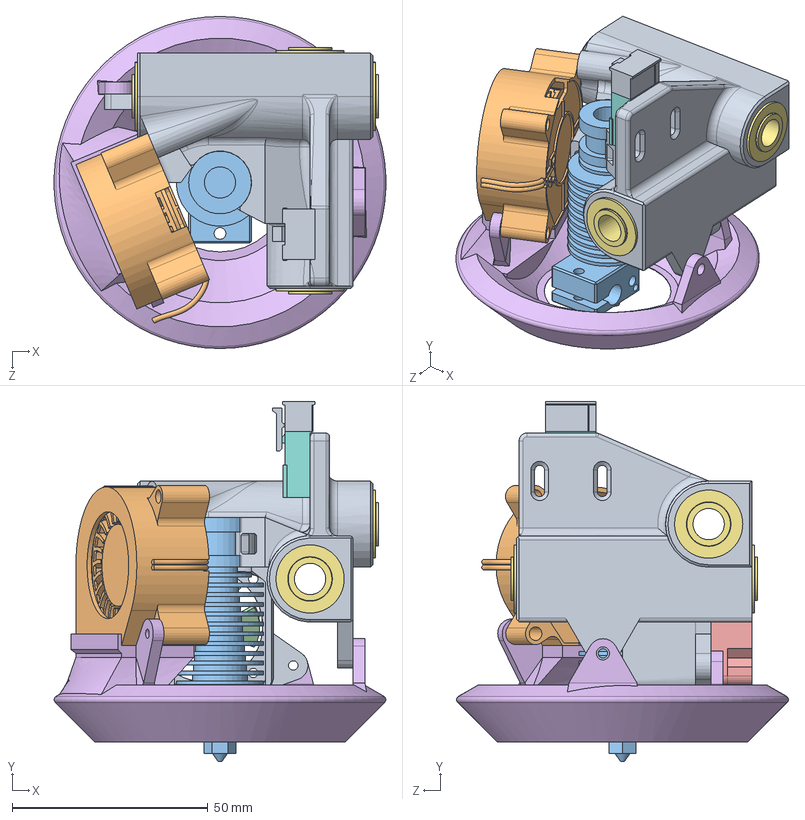
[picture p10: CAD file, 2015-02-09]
Solidworks Models/Sub Assemblies/Carriage Module V4/Eustathios_Carriage_V4_Molex_Microfit_3.SLDASM
84.7 x 91.9 x 84.7 mm
Carriage_V4_Molex_Microfit_3
4020Blower
E3D_V6
D3010_SOLID_1
D3010_QUILT_1
a_7z41mpsb08m x 4
Molex_430200801
Molex_430250800

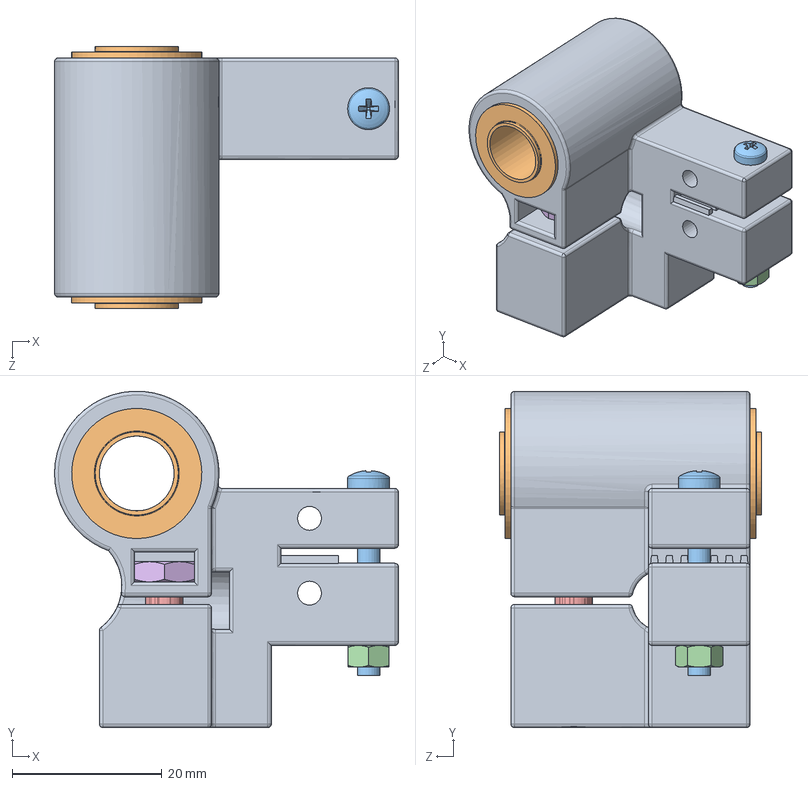
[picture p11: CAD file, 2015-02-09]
Solidworks Models/Sub Assemblies/XY Axis B Module/XY_Axis_Belt_Tensioner_B.SLDASM
46.0 x 45.0 x 35.0 mm
XY Axis Belt Tensioner B
a_7z41mpsb10m x 2
3mmx25mm_Stainless_Machine_Bolt
3mm_Hex_Nut
5mmx16mm_Stainless_Button_Head_Bolt
5mm_Hex_Jamnut

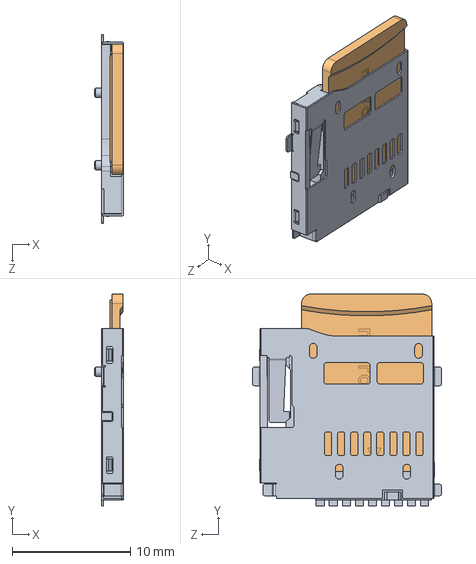
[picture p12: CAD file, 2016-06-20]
Solidworks/Electronics/Amazon/Raspberry Pi/raspberry_pi_B+_(microsd_slot).SLDASM
2.44 x 17.9 x 16.0 mm
raspberry_pi_B+_(slot)
raspberry_pi_B+_(microsd)

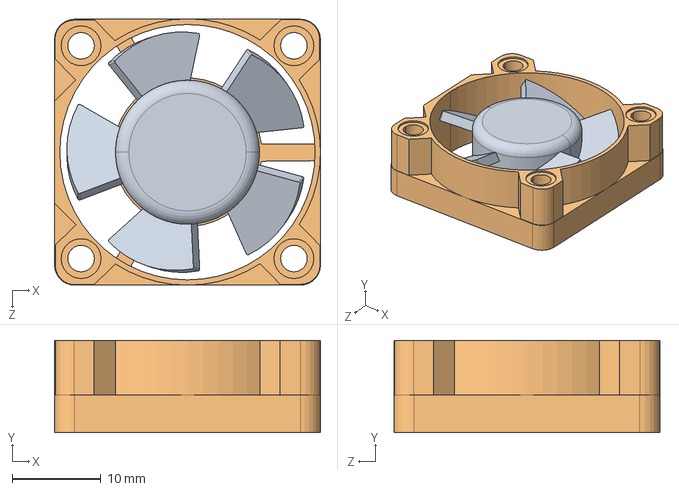
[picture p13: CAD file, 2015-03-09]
Solidworks/Electronics/E3D/30x30_Fan.SLDASM
30.0 x 10.4 x 30.0 mm
D3010_SOLID_1
D3010_QUILT_1

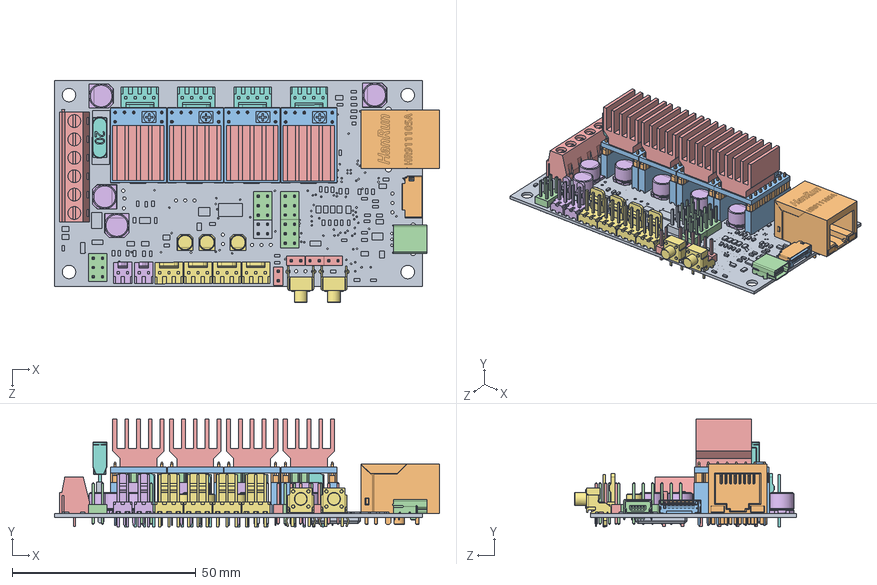
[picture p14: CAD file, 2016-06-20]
Solidworks/Electronics/Panucatt/X5miniV3/X5miniV3.SLDASM
104.7 x 29.2 x 60.3 mm
x5mv3 Board
User Library-HR911105A
female_header_a-bl254-eg-g08d x 8
2x3 Mhdr x 8
tblock 6pin
2x2 Mhdr
pin_header_aw140-eg-g08d x 8
SD5984_PCB x 4
pin_header_aw140-eg-g02d x 4
Panucatt Heatsink x 4
female_header (3pin)_a-bl254-eg-g08d x 4
c-1825027-8-g1-3d x 2
MINI Blade Fuse Type 2
Fuse Holder
usb_a-usb_b-m5-c
2x1 Mhdr x 4
Capacitor1 x 8
Capacitor2 x 3

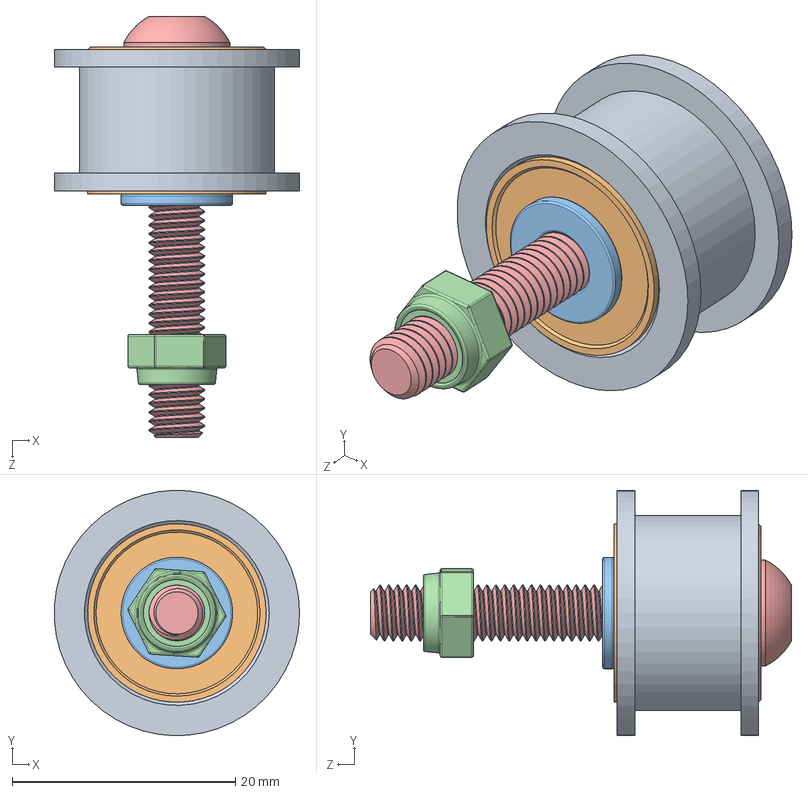
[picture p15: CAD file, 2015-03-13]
Solidworks/Hardware/OpenBuilds/Idler Wheel Assembly.SLDASM
22.0 x 22.0 x 37.8 mm
V-Slot Idler Pulley
Precision Ball Bearing x 2
5mm Precision Washer
Nylon Insert Hex Locknut 5mm
5mmX35mm_Buttonhead(McMaster_92095A220)
.125 Inch Aluminum Spacer

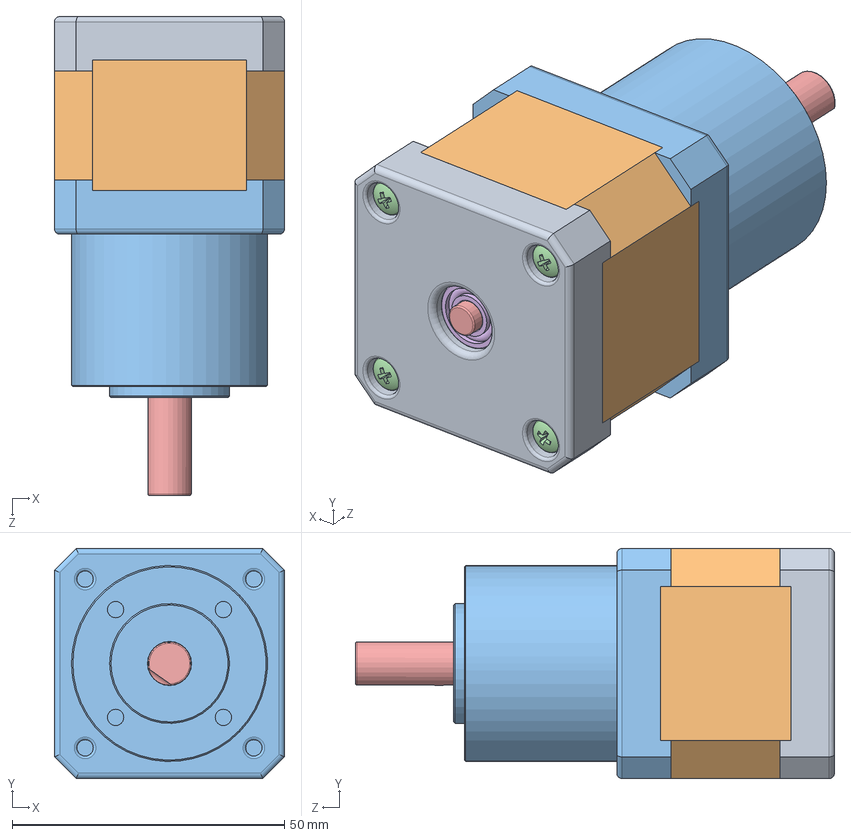
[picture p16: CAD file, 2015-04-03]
Solidworks/Robotdigg/NEMA_17_5.18_Planetary.SLDASM
42.3 x 42.3 x 88.0 mm
Base_Planetary
Body_Planetary
FaceCap_Planetary
pan cross head_am x 4
Shaft_Planetary
instrument ball bearing_68_am x 2

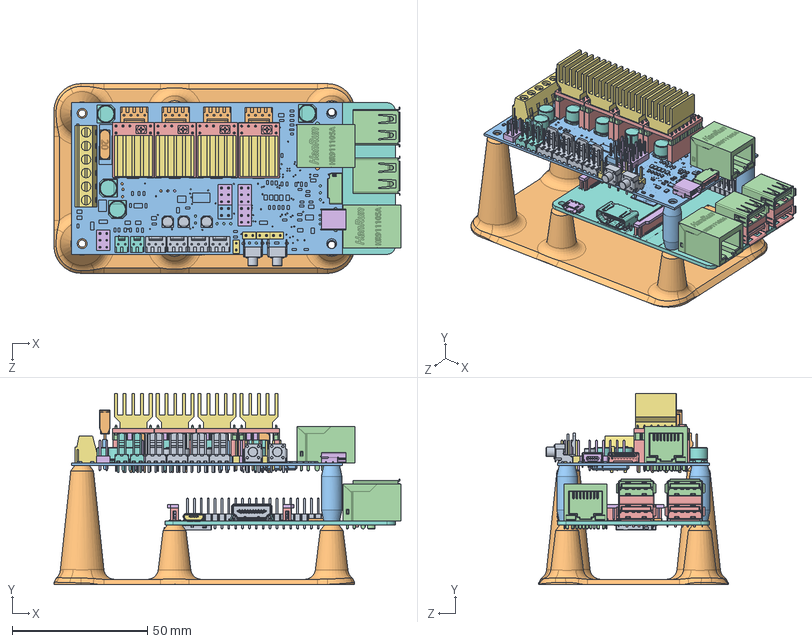
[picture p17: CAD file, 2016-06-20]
Solidworks/Sub Assemblies/Electronic_Package_(V5_Over_Under).SLDASM
128.1 x 70.7 x 70.0 mm
raspberry_pi_B+_(bar_180_2x20)
raspberry_pi_B+_(QFN64)
raspberry_pi_B+_(168_FBGA_12x12)
raspberry_pi_B+_(USB_x2_part1) x 2
raspberry_pi_B+_(USB_x2_part2) x 2
raspberry_pi_B+_(micro_USB_cover)
raspberry_pi_B+_(micro_USB_contacts)
raspberry_pi__HDMI_socket_cover
raspberry_pi__HDMI_socket_inside
raspberry_pi__HDMI_socket_large_pin x 10
raspberry_pi__HDMI_socket_small_pin x 9
raspberry_pi_B+_(RJ45)
raspberry_pi__15_pin_FFC_Connector_body x 2
raspberry_pi__15_pin_FFC_Connector_locker x 2
raspberry_pi__15_pin_FFC_Connector_pins x 30
raspberry_pi_B+_(CI_Board)
raspberry_pi_B+_(slot)
raspberry_pi_B+_(microsd)
x5mv3 Board
User Library-HR911105A
female_header_a-bl254-eg-g08d x 8
2x3 Mhdr x 8
tblock 6pin
2x2 Mhdr
pin_header_aw140-eg-g08d x 8
SD5984_PCB x 4
pin_header_aw140-eg-g02d x 4
Panucatt Heatsink x 4
female_header (3pin)_a-bl254-eg-g08d x 4
c-1825027-8-g1-3d x 2
MINI Blade Fuse Type 2
Fuse Holder
usb_a-usb_b-m5-c
2x1 Mhdr x 4
Capacitor1 x 8
Capacitor2 x 3
Electronic_Package_Mount V5 (Azteeg_X5 Mini V3 Stacked)
Electronic_Package_Mount Standoff V5 (Azteeg_X5 Mini V3 Stacked) x 2

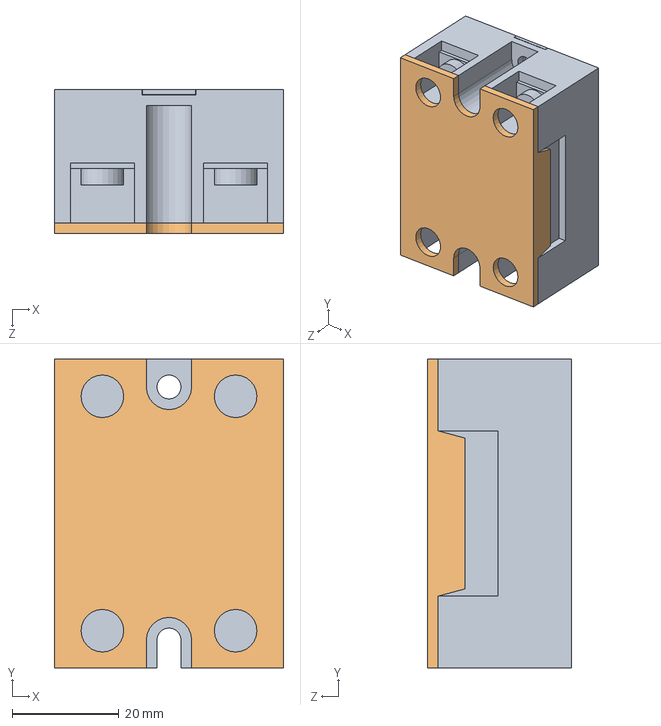
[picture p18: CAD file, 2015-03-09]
Solidworks/Electronics/Amazon/G3N_220B_SSR.SLDASM
43.0 x 58.0 x 27.0 mm
G3N_220B_SSR
G3N_220B_Cover

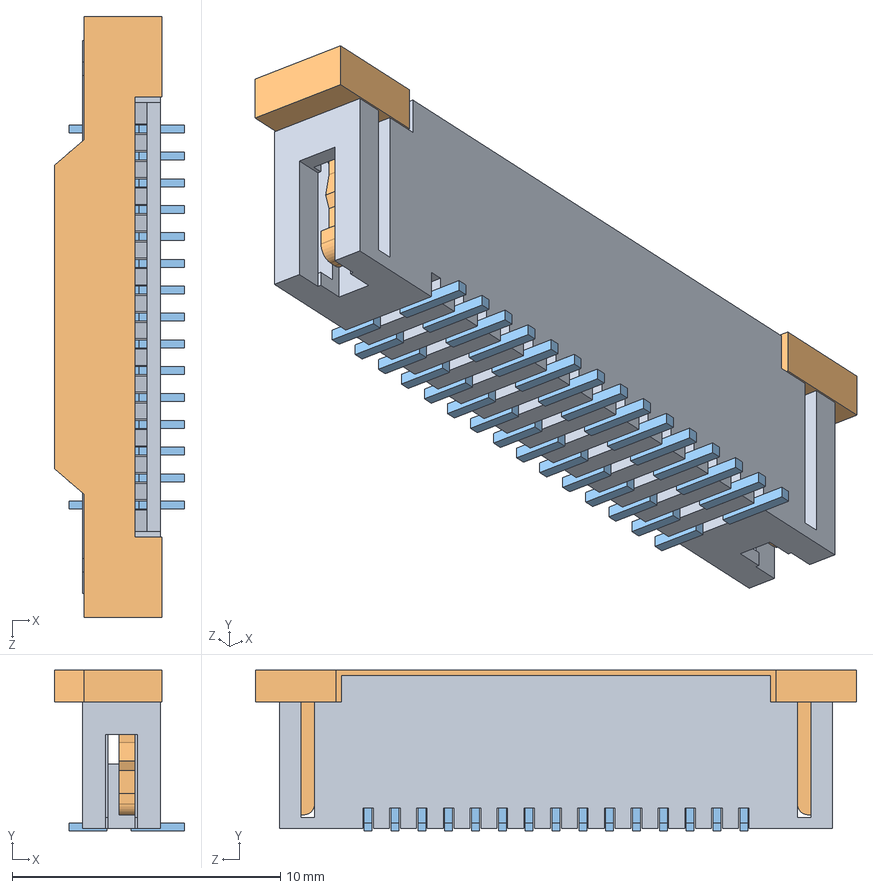
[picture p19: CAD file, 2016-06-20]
Solidworks/Electronics/Amazon/Raspberry Pi/raspberry_pi_B+_(15_pin_FFC_Connector).SLDASM
4.85 x 6.00 x 22.4 mm
raspberry_pi__15_pin_FFC_Connector_body
raspberry_pi__15_pin_FFC_Connector_locker
raspberry_pi__15_pin_FFC_Connector_pins x 15

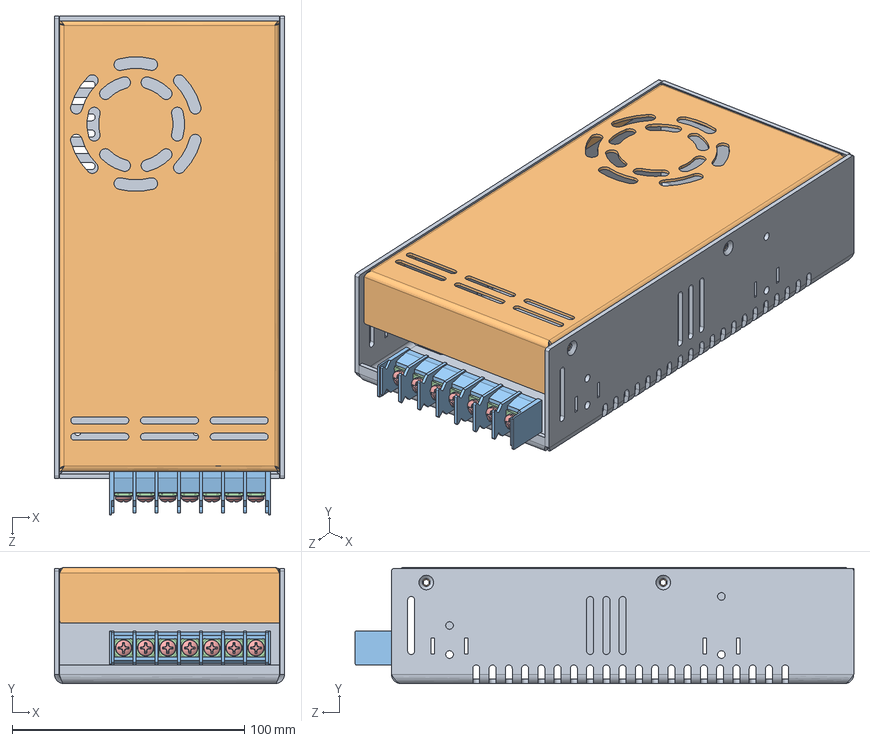
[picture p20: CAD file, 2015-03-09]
Solidworks/Electronics/Mean Well/Meanwell_SP-200-24.SLDASM
99.0 x 50.0 x 214.6 mm
Meanwell_SP-200-24_Housing1
Meanwell_SP-200-24_Housing2
Meanwell_SP-200-24_Terminal_Block
Clamp Plate Terminal Block x 7
Philips-Drive Panhead Screw Terminal Block x 7

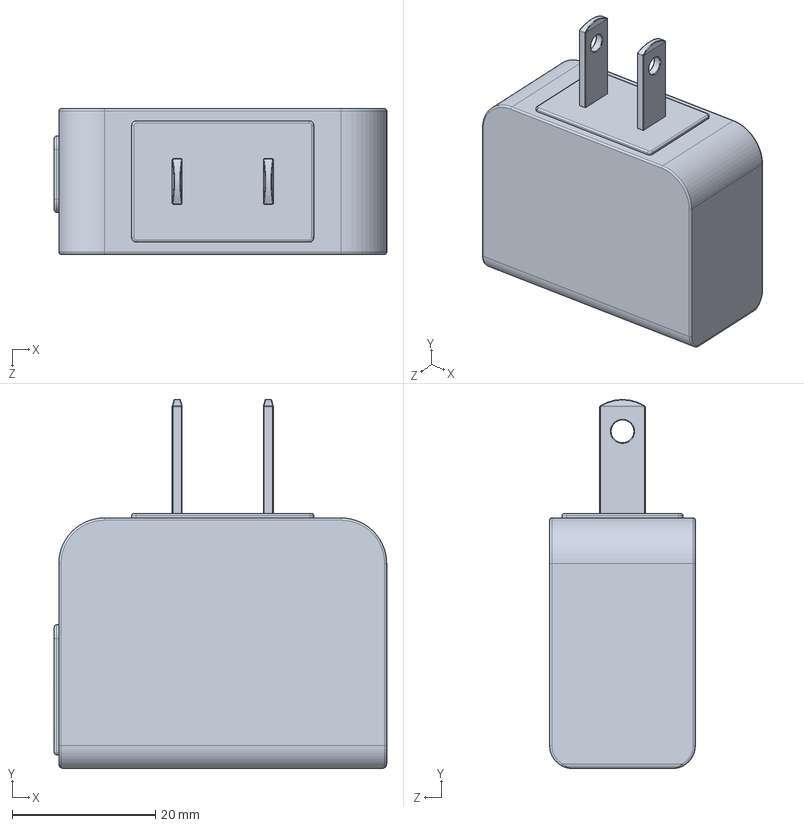
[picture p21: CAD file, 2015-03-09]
Solidworks/Electronics/Misc/Charger Assembly.SLDASM
46.4 x 51.4 x 20.3 mm
Charger Body
LG Phone Charger USB Receptacles
LG Phone Charger USB Connector

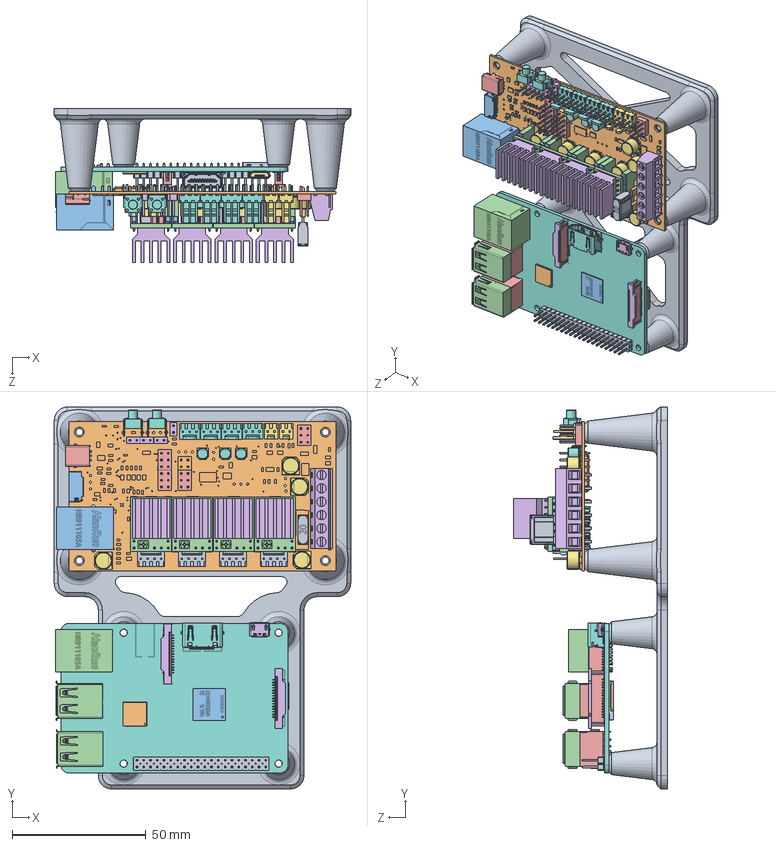
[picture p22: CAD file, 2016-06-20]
Solidworks/Sub Assemblies/Electronic_Package_(V4_side_by_side).SLDASM
111.0 x 143.0 x 57.7 mm
Electronic_Package_Mount (Azteeg_X5 Mini V3)
x5mv3 Board
User Library-HR911105A
female_header_a-bl254-eg-g08d x 8
2x3 Mhdr x 8
tblock 6pin
2x2 Mhdr
pin_header_aw140-eg-g08d x 8
SD5984_PCB x 4
pin_header_aw140-eg-g02d x 4
Panucatt Heatsink x 4
female_header (3pin)_a-bl254-eg-g08d x 4
c-1825027-8-g1-3d x 2
MINI Blade Fuse Type 2
Fuse Holder
usb_a-usb_b-m5-c
2x1 Mhdr x 4
Capacitor1 x 8
Capacitor2 x 3
raspberry_pi_B+_(bar_180_2x20)
raspberry_pi_B+_(QFN64)
raspberry_pi_B+_(168_FBGA_12x12)
raspberry_pi_B+_(USB_x2_part1) x 2
raspberry_pi_B+_(USB_x2_part2) x 2
raspberry_pi_B+_(micro_USB_cover)
raspberry_pi_B+_(micro_USB_contacts)
raspberry_pi__HDMI_socket_cover
raspberry_pi__HDMI_socket_inside
raspberry_pi__HDMI_socket_large_pin x 10
raspberry_pi__HDMI_socket_small_pin x 9
raspberry_pi_B+_(RJ45)
raspberry_pi__15_pin_FFC_Connector_body x 2
raspberry_pi__15_pin_FFC_Connector_locker x 2
raspberry_pi__15_pin_FFC_Connector_pins x 30
raspberry_pi_B+_(CI_Board)
raspberry_pi_B+_(slot)
raspberry_pi_B+_(microsd)

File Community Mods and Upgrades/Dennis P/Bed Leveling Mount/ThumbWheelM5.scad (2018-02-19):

$fn=80;
// radius of thumbwheel
rw=18.5;
// hight of thumbwheeel
hw=3;

//size of nut
rm4_ac=8.2/2/cos(360/12)-0.1;
// height of the nut
hm4=5;
// hole for the screw to go through without toughing
rm4free=5.25/2;
// hight of nut trapp 90% of nut height
h1=hm4*.9;
// outer radius of nut trapp
r1=rm4_ac+1.5;

//scale in or out
scale_type=2; //1=out 2=in

//height of scale
hs=.8;
//width of scale
ws=.6;
// number of major ticks
nm=4;
// small number for overlapp
e=0.01;
e2=1.4;
echo(hw+h1);

grip=30;
grip_gap=2;
grip_depth=0.8;
grip_angle=45;

module Grip() {
    rotate([grip_angle,0,0]) cube([1,grip_gap,hw*2],center=true); 
    rotate([-grip_angle,0,0]) cube([1,grip_gap,hw*2],center=true); 
}
module Grip2() {
    for (angle=[-grip_angle,grip_angle]) {
    hull(){
    rotate([angle,0,0]) cube([grip_depth*2,0.1,hw*2],center=true); 
    rotate([angle,0,0]) translate([1,0,0]) cube([1,grip_gap,hw*2],center=true); 
    }
}
}

module Scale() {
	for(i=[0:nm-1])
		rotate(360/nm*i)
			translate([r1,-ws/2,hw+1.5])cube([(rw-r1)-1,ws,hs]);
	for(i=[0:nm*2-1])
		rotate(360/nm/2*i)
			translate([r1+1+((rw-r1)-2)/2+1,-ws/2,hw+1.5])cube([((rw-r1)-2)/4,ws,hs]);
	for(i=[0:nm*10-1])
		rotate(360/nm/10*i)
			translate([r1+1+((rw-r1)-2)/4*3,-ws/2,hw+1.5])cube([((rw-r1)-2)/4,ws,hs]);
    
    	for(i=[0:nm-1])
		rotate(360/nm*(i+0.5)) {
           translate([r1+4.25,0,hw+1.5]) rotate([0,0,90]) linear_extrude(height = hs) text(text = str(i*2),font="Swis721 BT:style=Bold", size=5, halign="center", valign="center");
//            translate([r1+3.5, 0, hw+1.5]) rotate([0,0,90]) linear_extrude(height = hs) text(text = "\u2191  \u2191" ,size=5.75, halign="center", valign="center");
//            translate([r1+4.25, 0, hw+1.5]) rotate([0,0,90]) linear_extrude(height = hs) text(text = " -     +" ,size=5, halign="center", valign="center");
//           translate([r1+0.5+((rw-r1)-2)/2,-6.3, hw+1.5]) rotate([0,0,90]) linear_extrude(height = hs) text(text = "-   +" , font="Swis721 BT:style=Bold", size=5, halign="center", valign="center");
//    
//    translate([0,0,0]) rotate([0,0,0]) text("+\u2191 -\u2193", size=5, halign="center", valign="center" );  

            
        }
	
    }
    
module ThumbWheelM5(){
	//color("lime")
	difference(){
		union(){
			cylinder(hw,rw,rw,$fn=nm*30);
			translate([0,0,hw-e-e2])cylinder(h1+e,r1+2,r1);
            translate ([0,0,-1.5]) cylinder (h=1.5,r1=rw-1.5,r2=rw,$fn=64);
            translate ([0,0,hw])cylinder(h=1.5,r1=rw,r2=rw-1.5,$fn=64);
 		}
		translate([0,0,hm4-1.3])cylinder(hw+h1+2,rm4free,rm4free,$fn=24);
		translate([0,0,-1.5])cylinder(hm4,rm4_ac,rm4_ac,$fn=6);
//		translate([0,0,hw-e2])cylinder(hm4,rm4_ac,rm4_ac,$fn=6);

 
        for (i=[0:grip]) {
            rotate([0,0,360/grip*i]) translate([rw+0.5-grip_depth,0,hw/2]) Grip2(); 
        }
	if(scale_type==2) {
       translate([0,0,-hs+0.02]) Scale();
    }
        }
        if(scale_type==1) {
            color("black"){
	Scale();
            }
        }
}

translate([0,0,-16.4]) rotate([0,0,45]) ThumbWheelM5();

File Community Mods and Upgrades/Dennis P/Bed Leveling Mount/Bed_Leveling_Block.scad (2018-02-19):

// Eustahios version 2 Bed Leveling Block 
// remixed to include annotation 
//
// Uncommnet the line below to include the Thumbwheel
//include <ThumbwheelM5.scad>;
// 
// variables to control text placement
et=9.25;
//depth of text
dt=0.8;
//
difference () {
// MAIN BODY
   translate([-.75,0,0]) cube (size=[21.5,40,20], center = true);
// M5 CAP SCREW ANCHORS
    translate([5.5, 11,0]) rotate([0,90,0]) cylinder ($fn=90, h=5.5, r1=9.75/2, r2=9.75/2, center=false);
    translate([5.5,-11,0]) rotate([0,90,0]) cylinder ($fn=90, h=5.5, r1=9.75/2, r2=9.75/2, center=false);
    translate([-12.5,-11,0]) rotate([0,90,0]) cylinder ($fn=90, h=20, r1=5.05/2, r2=5.05/2, center=false);
    translate([-12.5, 11,0]) rotate([0,90,0]) cylinder ($fn=90, h=20, r1=5.05/2, r2=5.05/2, center=false);
// SPRING CORE HOLE
    translate([0,0,-10]) rotate([0,0,0]) cylinder ($fn=90, h=20, r1=5.05/2, r2=5.05/2, center=false);
    translate([0,0,6]) rotate([0,0,0]) cylinder ($fn=90, h=11, r1=12.6/2, r2=12.55/2, center=false);
//BROAD FACE TEXT
    translate([et, 0,-5.7]) rotate([90,0,90]) linear_extrude(height = dt) text(text = "|" ,size=5.75, halign="center", valign="center");
    translate([et, -14,-6.7]) rotate([90,0,90]) linear_extrude(height = dt) text(text = "\u2190" ,size=12, halign="center", valign="center");
     translate([et, 14,-6.7]) rotate([90,0,90]) linear_extrude(height = dt) text(text = "\u2192" ,size=12, halign="center", valign="center");
     translate([et, 4.5,-6.8]) rotate([90,0,90]) linear_extrude(height = dt) text(text = "\u002B" ,size=8, halign="center", valign="center");
     translate([et, -4.5,-7.6]) rotate([90,0,90]) linear_extrude(height = dt) text(text = "\u002D" ,size=8, halign="center", valign="center");
    translate([et, 0,7.3]) rotate([90,0,90]) linear_extrude(height = dt) text(text = "NOZZLE / BED" ,size=4, halign="center", valign="center");
    translate([et, 0,1.75]) rotate([90,0,90]) linear_extrude(height = dt) text(text = "GAP" ,size=4, halign="center", valign="center");
//  This is sized for narrow 5.25mm slots, a la 8020.net extrusions    
    translate([-11.5,-20, 5.5/2]) cube (size=[1.5,40,7.25], center=false);
    translate([-11.5,-20, -10]) cube (size=[1.5,40,7.25], center=false);
//  This is sized for 6mm slots    
//    translate([-11.5,-20, 6/2]) cube (size=[1.5,40,7], center=false);
//    translate([-11.5,-20, -10]) cube (size=[1.5,40,7], center=false);
//
//RIGHT END TEXT 
//    translate([3, 20-.8,-7.5]) rotate([90,0,180]) linear_extrude(height = 0.8) text(text = "\u2194" ,size=5.75, halign="center", valign="center");
// translate([10, 20-.8,-7.5]) rotate([90,0,180]) linear_extrude(height = 0.8) text(text = "-    +" ,size=5.75, halign="LEFT", valign="center");
//    translate([11, 20-.8,3.5]) rotate([90,0,180]) linear_extrude(height = 0.8) text(text = "NOZZLE" ,size=4, halign="LEFT", valign="center");
//    translate([11, 20-.8,-2.5]) rotate([90,0,180]) linear_extrude(height = 0.8) text(text = "BED GAP" ,size=4, halign="LEFT", valign="center");
//
// LEFT END TEXT
//    translate([-12.5, -20+.8,3.5]) rotate([90,0,0]) linear_extrude(height = 0.8) text(text = "NOZZLE" ,size=4, halign="LEFT", valign="center");
//    translate([-12.5, -20+.8,-2.5]) rotate([90,0,0]) linear_extrude(height = 0.8) text(text = "BED GAP" ,size=4, halign="LEFT", valign="center");
//        translate([2, -20+.8,-7.5]) rotate([90,0,0]) linear_extrude(height = 0.8) text(text = "\u2194" ,size=5.75, halign="center", valign="center");
//    translate([-5, -20+.8,-7.5]) rotate([90,0,0]) linear_extrude(height = 0.8) text(text = "-    +" ,size=5.75, halign="LEFT", valign="center");
}
// translate([0, 0,-20]) rotate([0,0,0]) ThumbwheelM5();

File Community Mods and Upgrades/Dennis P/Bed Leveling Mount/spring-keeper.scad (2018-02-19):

$fn=80;
// ID of spring keeper
id=0.55*25.4;
//wall thickness
tw=2;
// height of springkeep
hw=4;
//base of spring kepper
tb=1.5;
// hole for the screw to go through
rm4free=5.25/2;
//size of nut
rm4_ac=8.2/2/cos(360/12)-0.1;
// height of the nut
hm4=5.5;

	difference(){
	cylinder($fn=90,h=hw+tb+hm4,r=id/2+tw,center=false);
    translate([0,0,hm4])  cylinder($fn=90, h=hw+hm4, r=id/2, center=false);
//    translate ([0,0,0]) cylinder($fn=90, h=hw+tb+hm4, r1=rm4free, center=false);
	translate([0,0,0]) cylinder(hm4,rm4_ac,rm4_ac,$fn=6);
}

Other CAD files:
Solidworks/Electronics/Ultimachines/Jamicon_KF0410-01.SLDASM
Solidworks/Robotdigg/NEMA_17_60mm_1.5A.SLDASM
Community Mods and Upgrades/Eric Lien/Compact Carriage with BLTouch/BLTouch.sldasm
Solidworks/Electronics/Amazon/Raspberry Pi/raspberry_pi_B+_(slot).SLDASM
Community Mods and Upgrades/Dennis P/8020_20x20_Cable Clips/Cable Ring Low.stl
Community Mods and Upgrades/Dennis P/8020_20x20_Cable Clips/Cable Ring.stl
Community Mods and Upgrades/Dennis P/Bed Leveling Mount/Bed_Leveling_Block_5.25mm_Slot.stl
Community Mods and Upgrades/Dennis P/Bed Leveling Mount/Bed_Leveling_Block_6mm_Slot.stl
Community Mods and Upgrades/Dennis P/Bed Leveling Mount/ThumbWheelM5.stl
Community Mods and Upgrades/Dennis P/Bed Leveling Mount/block-text-test.stl
Community Mods and Upgrades/Dennis P/Bed Leveling Mount/spring-keeper.stl
Community Mods and Upgrades/Dennis P/Belt Tensioner/belt-tensioner_Left.stl
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

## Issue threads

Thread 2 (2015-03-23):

Tensioner nut hole needs to be larger

benjamind, 2015-03-23:
I just tried assembling the Z-axis leadscrew support with the tensioner idler. Its really hard to get the locking nylon nut into place and tight since they're hard to hold with needle nose pliers and the hole for the nut is too small to fit a standard socket driver into. In the end I drilled it out with a 12mm drill bit to make it large enough to fit the socket driver into.

I'd suggest widening the hole for that nut to something like 12mm minimum to allow for drivers to get in there easily. Possibly this could also apply to the other nut holes on these mounts.

eclsnowman, 2015-03-23:
Odd. I was able to fit the socket on mine. I must have a socket with
thinner walls. I will look into it tonight.
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

benjamind, 2015-03-23:
Its really really close, so its probably small deviations in socket manufacturer I guess.

Looking great though, just need my extrusion to arrive!

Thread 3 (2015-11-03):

Thoughts on a Core XY Version?

NullVoxPopuli, 2015-11-03:
corexy seems to be the best way of moving the x/y axis. Are there plans to modify this design to work with that?

justinledwards, 2015-11-03:
Best in what way?

NullVoxPopuli, 2015-11-03:
equal tension in all x/y directions -- which allows for faster, more accurate prints

justinledwards, 2015-11-03:
It's less constrained and relies on more things to have tighter tolerances and usually doesn't incorporate any preloading, which makes it print less well, and has to run slower to get good results.

The proof is in the end product.

eclsnowman, 2015-11-03:
Nope. I guess I disagree corexy is best. Mostly because I designed and ran
one before. Infact Herculien is based on the frame of my old corexy. I
moved to this ingentis/ultimaker style gantry design. I am much happier
than I was with corexy, and it has required no maintenance in almost 2
years so it is more repeatable than my corexy ever was.

On Tue, Nov 3, 2015 at 8:15 AM, L. Preston Sego III <
notifications@github.com> wrote:

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

Closed 2017-09-29.

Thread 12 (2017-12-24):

price in BOM

icebal, 2017-12-24:
is there a price quote for the BOM? the second page looks like it, since quanity doesnt add up.

eclsnowman, 2017-12-25:
Cost really depends on how you source the parts. There are cheaper ways to do it and more expensive ones. There is no definitive BOM cost sheet, but I am always open if someone is willing to make one. Only the list of parts and the vendors I used. But Some people started to make it into a google document which added some links:

https://docs.google.com/spreadsheets/d/1ATz5AoIUtASowBtlXsOb8FVt8YLd0A-wu1EWHHHPDnA/edit?usp=sharing

icebal, 2017-12-27:
thanks! that helps a lil bit more :)
so far the only thing i'm seeing that isn't working is the lead screws. for part MTSBRB12-425-S46-Q8-C3-J0 mitsumi will not allow a 0 value for J, only 2-41 with the s/q/c values you have listed on the keyed shaft. does J need to be 0? or can i get away with 2mm J? the values they have are MTSBRB12-[80-1000/1]-S[2-63/1]-Q[7, 8, 9]-C[3-60/1]-J[2-61/1]

eclsnowman, 2017-12-27:
I would check these out instead:

SFU1204 - L425mm   1pc RM1204 Ballscrew Ballnut for 12mm screw rail

 http://s.aliexpress.com/EJZNB7bQ?

Just make sure to mention the ball nut needs to be per the picture.

On Dec 27, 2017 10:36 AM, "wesley jackson" <notifications@github.com> wrote:

thanks! that helps a lil bit more :)
so far the only thing i'm seeing that isn't working is the lead screws. for
part MTSBRB12-425-S46-Q8-C3-J0 mitsumi will not allow a 0 value for J, only
2-41 with the s/q/c values you have listed on the keyed shaft. does J need
to be 0? or can i get away with 2mm J? the values they have are
MTSBRB12-[80-1000/1]-S[2-63/1]-Q[7, 8, 9]-C[3-60/1]-J[2-61/1]

—
You are receiving this because you commented.

Reply to this email directly, view it on GitHub
<https://github.com/eclsnowman/Eustathios-Spider-V2/issues/12#issuecomment-354139597>,
or mute the thread
<https://github.com/notifications/unsubscribe-auth/AB-RmyMx53qO-J9cDSxbrjngICfWPaYqks5tEnH1gaJpZM4RMBDI>
.

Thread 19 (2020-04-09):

Missing Model from the BlTouchEustathios.SLDASM

kesjeff, 2020-04-09:
HI Eric,

When I opened this assembly up this model was missing from the repository.

C:\Users\ronij\Documents\3D printing\Herculien-Solidworks\molex_microfit_female_containment.SLDPRT

Thanks,
Jeff Kes

eclsnowman, 2020-04-09:
That one came from Zane Baird. I have just contacted Zane to see if he can push the file into the directory.

kesjeff, 2020-04-09:
Awesome thanks

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

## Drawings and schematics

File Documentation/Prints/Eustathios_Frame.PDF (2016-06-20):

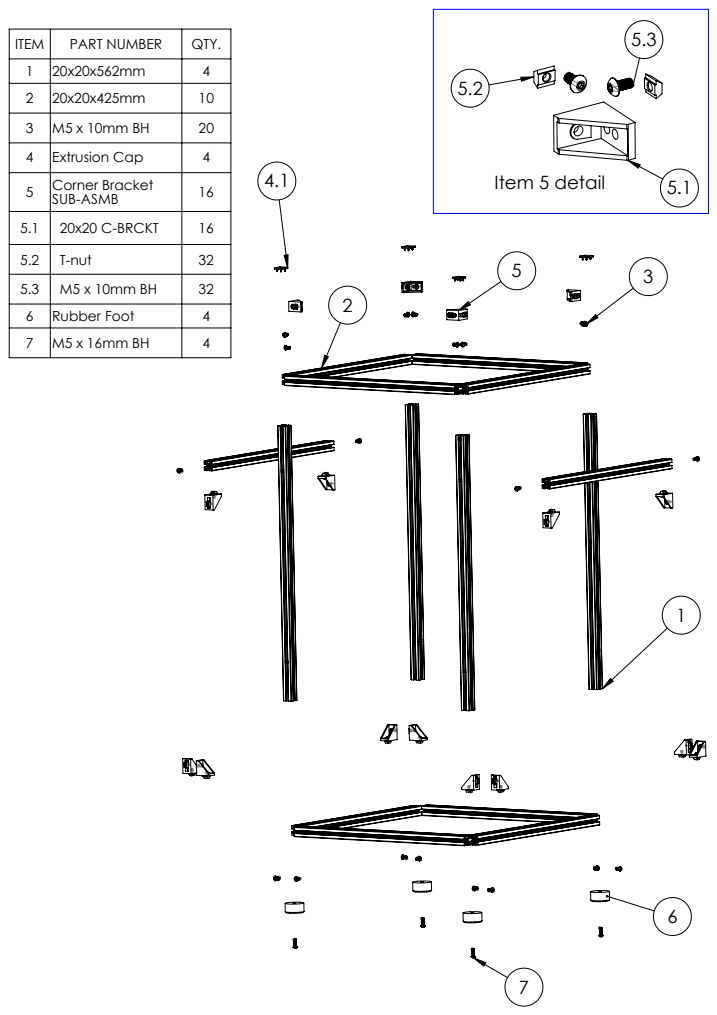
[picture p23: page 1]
Item 5 detail

ITEM | PART NUMBER | QTY.
1 | 20x20x562mm | 4
2 | 20x20x425mm | 10
3 | M5 x 10mm BH | 20
4 | Extrusion Cap | 4
5 | Corner Bracket SUB-ASMB | 16

5.1 | 20x20 C-BRCKT | 16
5.2 | T-nut | 32
5.3 | M5 x 10mm BH | 32
6 | Rubber Foot | 4
7 | M5 x 16mm BH | 4

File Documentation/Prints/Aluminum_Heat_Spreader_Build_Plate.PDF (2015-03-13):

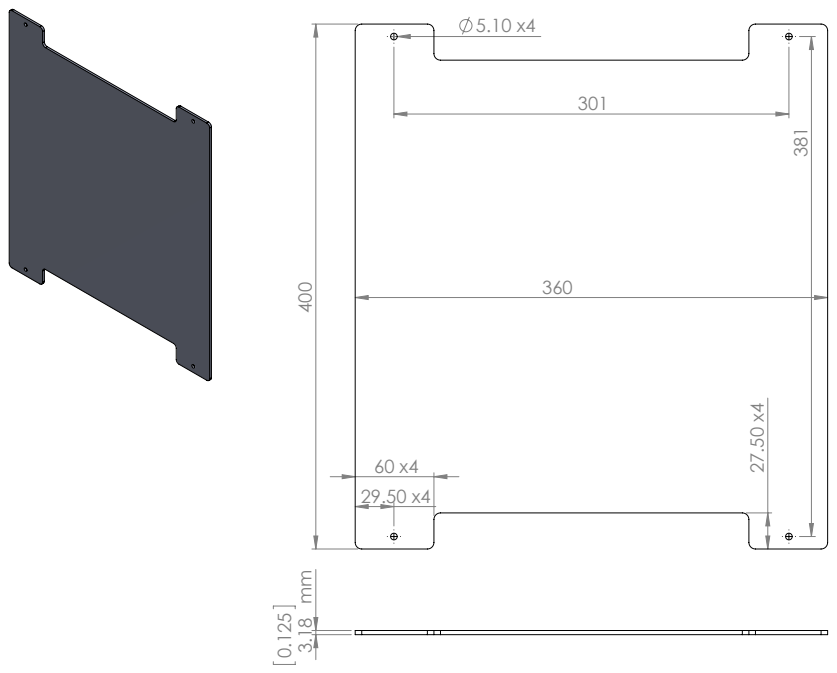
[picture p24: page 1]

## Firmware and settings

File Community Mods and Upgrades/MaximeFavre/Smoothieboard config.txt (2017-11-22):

Config file for Eustathios V2 running on original smoothieboard and latest edge firmware (22.11.2017)

Setup used:
- I use walter's carriage. hotend fan is always powered so no switch config
  Parts fans are on 2.4 with PWM
- no bed probe, a well levelled bed is all you need ;)
- hotend on 2.7, sensor 0.23
- bed on 2.6, sensor 0.24
- bondtech extruder (you may need to adjust step/mm if you use another one)
- viki2 LCD wired as follow:
    SDCD to P0.27
    BTN to P1.30
    SDCS to P2.8
    LCS to P0.16
    SCK to P0.15
    GND to 5v power supply's ground or a ground pin on the smoothieboard
    ENCB to P3.26
    ENCA to P3.25
    MISO to P0.8
    A0 to P2.11
    MOSI to P0.18
    =Vin to 5v power supply

    BTN to None, Viki 2.0 has 2 Blue BTN wires that do the same thing
    Buzzer to P1.31
    Blue-LED to P1.23
    Red-LED to P1.22
**I don't use red/blue led in this config




# Smoothieboard configuration file, see http://smoothieware.org/configuring-smoothie
# NOTE Lines must not exceed 132 characters, and '#' characters mean what follows is ignored
## Robot module configurations : general handling of movement G-codes and slicing into moves

# Basic motion configuration
default_feed_rate                            4000             # Default speed (mm/minute) for G1/G2/G3 moves
default_seek_rate                            4000             # Default speed (mm/minute) for G0 moves
mm_per_arc_segment                           0.0              # Fixed length for line segments that divide arcs, 0 to disable
#mm_per_line_segment                         5                # Cut lines into segments this size
mm_max_arc_error                             0.01             # The maximum error for line segments that divide arcs 0 to disable
                                                              # note it is invalid for both the above be 0
                                                              # if both are used, will use largest segment length based on radius

# Arm solution configuration : Cartesian robot. Translates mm positions into stepper positions
# See http://smoothieware.org/stepper-motors
alpha_steps_per_mm                           80               # Steps per mm for alpha ( X ) stepper
beta_steps_per_mm                            80               # Steps per mm for beta ( Y ) stepper
gamma_steps_per_mm                           1280             # Steps per mm for gamma ( Z ) stepper

# Planner module configuration : Look-ahead and acceleration configuration
# See http://smoothieware.org/motion-control
acceleration                                 9000             # Acceleration in mm/second/second.
z_acceleration                              300              # Acceleration for Z only moves in mm/s^2, 0 uses acceleration which is the default. DO NOT SET ON A DELTA
junction_deviation                           0.05             # See http://smoothieware.org/motion-control#junction-deviation
#z_junction_deviation                        0.0              # For Z only moves, -1 uses junction_deviation, zero disables junction_deviation on z moves DO NOT SET ON A DELTA

# Cartesian axis speed limits
x_axis_max_speed                             30000            # Maximum speed in mm/min
y_axis_max_speed                             30000            # Maximum speed in mm/min
z_axis_max_speed                             300              # Maximum speed in mm/min

# Stepper module configuration 
# Pins are defined as  ports, and pin numbers, appending "!" to the number will invert a pin
# See http://smoothieware.org/pin-configuration and http://smoothieware.org/pinout
alpha_step_pin                               2.0              # Pin for alpha stepper step signal
alpha_dir_pin                                0.5!              # Pin for alpha stepper direction, add '!' to reverse direction
alpha_en_pin                                 0.4              # Pin for alpha enable pin
alpha_current                                1.5              # X stepper motor current
alpha_max_rate                               30000.0          # Maximum rate in mm/min

beta_step_pin                                2.1              # Pin for beta stepper step signal
beta_dir_pin                                 0.11             # Pin for beta stepper direction, add '!' to reverse direction
beta_en_pin                                  0.10             # Pin for beta enable
beta_current                                 1.5              # Y stepper motor current
beta_max_rate                                30000.0          # Maxmimum rate in mm/min

gamma_step_pin                               2.2              # Pin for gamma stepper step signal
gamma_dir_pin                                0.20             # Pin for gamma stepper direction, add '!' to reverse direction
gamma_en_pin                                 0.19             # Pin for gamma enable
gamma_current                                1.5              # Z stepper motor current
gamma_max_rate                               300.0            # Maximum rate in mm/min

## Extruder module configuration
# See http://smoothieware.org/extruder
extruder.hotend.enable                          true          # Whether to activate the extruder module at all. All configuration is ignored if false
extruder.hotend.steps_per_mm                    476.5         # Steps per mm for extruder stepper
extruder.hotend.default_feed_rate               600           # Default rate ( mm/minute ) for moves where only the extruder moves
extruder.hotend.acceleration                    1000           # Acceleration for the stepper motor mm/sec²
extruder.hotend.max_speed                       5000            # Maximum speed in mm/s

extruder.hotend.step_pin                        2.3           # Pin for extruder step signal
extruder.hotend.dir_pin                         0.22          # Pin for extruder dir signal ( add '!' to reverse direction )
extruder.hotend.en_pin                          0.21          # Pin for extruder enable signal

# Extruder offset
#extruder.hotend.x_offset                        0            # X offset from origin in mm
#extruder.hotend.y_offset                        0            # Y offset from origin in mm
#extruder.hotend.z_offset                        0            # Z offset from origin in mm

# Firmware retract settings when using G10/G11, these are the defaults if not defined, must be defined for each extruder if not using the defaults
#extruder.hotend.retract_length                  3            # Retract length in mm
#extruder.hotend.retract_feedrate                45           # Retract feedrate in mm/sec
#extruder.hotend.retract_recover_length          0            # Additional length for recover
#extruder.hotend.retract_recover_feedrate        8            # Recover feedrate in mm/sec (should be less than retract feedrate)
#extruder.hotend.retract_zlift_length            0            # Z-lift on retract in mm, 0 disables
#extruder.hotend.retract_zlift_feedrate          6000         # Z-lift feedrate in mm/min (Note mm/min NOT mm/sec)

delta_current                                    1.3          # First extruder stepper motor current


## Temperature control configuration
# See http://smoothieware.org/temperaturecontrol

# First hotend configuration
temperature_control.hotend.enable            true             # Whether to activate this ( "hotend" ) module at all.
temperature_control.hotend.thermistor_pin    0.23             # Pin for the thermistor to read
temperature_control.hotend.heater_pin        2.7              # Pin that controls the heater, set to nc if a readonly thermistor is being defined
temperature_control.hotend.thermistor        Semitec        # See http://smoothieware.org/temperaturecontrol#toc5
#temperature_control.hotend.beta             4066             # Or set the beta value
temperature_control.hotend.set_m_code        104              # M-code to set the temperature for this module
temperature_control.hotend.set_and_wait_m_code 109            # M-code to set-and-wait for this module
temperature_control.hotend.designator        T                # Designator letter for this module
#temperature_control.hotend.max_temp         300              # Set maximum temperature - Will prevent heating above 300 by default
#temperature_control.hotend.min_temp         0                # Set minimum temperature - Will prevent heating below if set

# Safety control is enabled by default and can be overidden here, the values show the defaults
# See http://smoothieware.org/temperaturecontrol#runaway
#temperature_control.hotend.runaway_heating_timeout      900  # How long it can take to heat up, max is 2040 seconds.
#temperature_control.hotend.runaway_cooling_timeout        0  # How long it can take to cool down if temp is set lower, max is 2040 seconds
#temperature_control.hotend.runaway_range                20   # How far from the set temperature it can wander, max setting is 63°C
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

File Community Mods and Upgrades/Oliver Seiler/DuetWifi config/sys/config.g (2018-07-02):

; Configuration file for Duet WiFi (firmware version 1.21)
; executed by the firmware on start-up

; General preferences
M111 S0 ; Debugging off
G21 ; Work in millimetres
G90 ; Send absolute coordinates...
M83 ; ...but relative extruder moves
M555 P2 ; Set firmware compatibility to look like Marlin
M208 X0 Y0 Z0 S1 ; Set axis minima
M208 X285 Y285 Z250 S0 ; Set axis maxima

; Endstops
M574 X1 Y1 Z1 S0 ; Define active low and unused microswitches
M558 P1 X0 Y0 Z0 H3 F120 T12000 ; Set Z probe type to unmodulated, the axes for which it is used and the probe + travel speeds
G31 P500 X0 Y0 Z0.84 ; Set Z probe trigger value, offset and trigger height
M557 X15:260 Y15:260 S20 ; Define mesh grid

; Drives
M569 P0 S1 ; Drive 0 goes forwards
M569 P1 S0 ; Drive 1 goes backwards
M569 P2 S0 ; Drive 2 goes backwards
M569 P3 S1 ; Drive 3 goes forwards
M569 P4 S1 ; Drive 4 goes forwards
M92 X100 Y100 Z800 E476:803 ; Set steps per mm
M350 X16 Y16 Z16 E16:16 I1 ; Configure microstepping with interpolation
M566 X500 Y500 Z60 E300:300 ; Set maximum instantaneous speed changes (mm/min)
M203 X12000 Y12000 Z1200 E3900:3600 ; Set maximum speeds (mm/min)
M201 X1500 Y1500 Z100 E1000:500 ; Set accelerations (mm/s^2)
M906 X1000 Y1000 Z800 E800:800 I30 ; Set motor currents (mA) and motor idle factor in per cent
M84 S300 ; Set idle timeout

; Heaters
M143 S280 ; Set maximum heater temperature to 280C
M305 P0 T100000 B3974 C0 R4700 ; Set thermistor + ADC parameters for heater 0
M305 P1 T100000 B4388 C0 R4700 ; Set thermistor + ADC parameters for heater 1
M305 P2 T100000 B4388 C0 R4700 ; Set thermistor + ADC parameters for heater 2

; Heater control
M307 H0 A90.0 C700.0 D10.0 S1.00 B1

; Allow cold extrusion
M302 P1

; Fans
M106 P0 S255 I0 F500 H1:2 T50 ; Set fan 0 (hotend cooling) value, PWM signal inversion and frequency. Thermostatic control for Heater 1 (and 2 :2)
M106 P1 S0 I0 F500 H-1 ; Set fan 1 (part cooling) value, PWM signal inversion and frequency. Thermostatic control is turned off
M106 P2 S0 I0 F500 H-1 ; Set fan 2 value, PWM signal inversion and frequency. Thermostatic control is turned off

; Tools
M563 P0 D0 H1 F1; Define tool 0
G10 P0 X0 Y0 Z0 ; Set tool 0 axis offsets
G10 P0 R0 S0 ; Set initial tool 0 active and standby temperatures to 0C
M563 P1 D1 H2 F1; Define tool 1
G10 P1 X-0.1 Y17.8 Z0 ; Set tool 1 axis offsets
G10 P1 R0 S0 ; Set initial tool 1 active and standby temperatures to 0C
M563 P2 D1 H1 F1; Define tool 2 - used for direct drive carriage with second extruder on first hotend (you probably do not want this)

; Network
M550 PEustathios Spider V2 ; Set machine name
M552 S1 ; Enable network
; Access point is configured manually via M587 by the user
M586 P0 S1 ; Enable HTTP
M586 P1 S0 ; Disable FTP
M586 P2 S0 ; Disable Telnet

; Custom settings are not configured

M929 S1 ;enable logging
M915 P0:1 S8 F1 H400 R3 ; log stall detection, S8 seems a good value.
M572 D0 S0 ;enable linear advance on E0
M572 D1 S0 ;enable linear advance on E1

; overwrite to 300x300 build size - use if needed.
;M208 X300 Y300 Z250 S0

; Heater PIDs
M307 H0 A90.0 C700.0 D10.0 S1.00 B1
M307 H1 A340.0 C140.0 D5.5 S1.00 B0
M307 H2 A708.6 C233.9 D9.0 S1.00 B0

M501 ; load config-overrige.g
 
; Miscellaneous
T0 ; Select first tool
M564 H0 ;allow movement without homing

; power loss auto save
M911 S20.0 R40.0 P"M913 X0 Y0 G91 M83 G1 Z3 E-5 F1000"

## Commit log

2015-02-09 First Upload, Please note this is a WIP
    First Upload, Please note this is a WIP
    [.75L_.5OD_.062Wire(McMaster_9657K292).SLDPRT, 10mm_Rod_End_Bearing_Assembly.SLDASM, 10mmx16mmx0.5mm_SHim(McMaster_90214A422).SLDPRT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]
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2015-02-24 Small changes to the Main Assembly
    Small changes to the main assembly, added a smaller PSU than on the V1
    Eustathios Spider (only 200W), added SSR to run the heated bed on 120V
    AC (or related mains voltage of the country).
    [Clamp Plate Terminal Block.SLDPRT, G3N_220B_Cover.SLDPRT, G3N_220B_SSR.SLDASM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]
2015-03-03 Z Drive Changes & Viki2
    Added an idler on the Z Leadscrew drive support/mounts to get more
    contact with the pulleys for better grip and now the belt works out
    better for use with the less expensive Robotdigg 976mm long belt.
    Added The Viki2 LCD mount for use with the Azteeg X5 mini. I have been
    testing this combo of electronics and LCD for several weeks and it is
    far superior to the 8bit solutions.
    [.125 Inch Aluminum Spacer.SLDPRT, 5mm Precision Washer.SLDPRT, 5mm x 25mm Low Profile Socket Head Screw.SLDPRT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]
2015-03-09 Cleanup and Reorganize Files
    Cleanup of folder structure and files preparing for Official Release.
    [.125 Inch Aluminum Spacer.SLDPRT, .75L_.5OD_.062Wire(McMaster_9657K292).SLDPRT, 1.5inX.75inX.25inHole_Foot(Mcmaster_9540K28).SLDPRT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]
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2015-03-12 More progress on BOM
    More formatting on BOM, Getting close to adding pricing. Please note the
    BOM is still a WIP... But it is getting close.
    [320x320x3mm_Glass_Print_Surface.SLDPRT, 360x345_Glass_Print_Surface.SLDPRT, Carriage_V4_Part_Cooling_Duct.sldprt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]
2015-03-13 Multiple Cad Formats, Print STLs, and BOM Changes
    I added 3D PDF, Designspark Mechanical, Edrawings, ProE, Rhino, Step,
    and X_T Files formats. I also cleaned up and formatted more of the BOM.
    I created the pritable STL's. I started by making the heat spreader
    plate print and dxf.
    I still plan to orient the STL's correctly, run them through netfab, and
    potentially match them into plates. But for now I am tired and need some
    sleep.
    [10mm_Rod_End_Bearing_Assembly.SLDASM, 1L_.5OD_.062Wire(McMaster_9657K313).SLDPRT, 320x320_120VAC_500W_Heated_Bed.SLDPRT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]
2015-03-20 Correct BOM and add Fusion 360
    Corrected a BOM description for one of the extrusions, and added a
    Fusion 360 version in the Other 3D Format folder.
    [Eustathios Spider V2 BOM.xlsx]
2015-04-03 Add Firmware Config
    Config File for Smoothieware setup on Azteeg X5 Mini
    [NEMA_17_5.18_Planetary.SLDASM]
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2015-05-15 Added DXF files for all panels
    Added DXF files for all panels so fabrication via CNC is easier. Also
    added a Z movement only Gcode breakin to help with z ribbing artifacts.
    Updated the electronic package mount to use less material (V2) and look
    more interesting. Fixed Z-lead screw support STLs since the diaphragms
    to allow printing without support were extruded the wrong way making
    them floating disks instead of bridges.
    [Acrylic_or_Polycarbonate_Back_Bottom.DXF, Acrylic_or_Polycarbonate_Front_Bottom.DXF, Acrylic_or_Polycarbonate_Left_Bottom.DXF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]
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2015-06-14 Small Updates
    Updated lower mount to allow socket to reach nut, updated Azteeg X5 mini
    smoothie config with better tuned PID, Notes about running LED from
    Octoprint.
    [Carriage_V4_Part_Cooling_Duct.sldprt, Z-Screw_Support_V2.SLDASM, Z_Axis_Leadscrew_Support_V2.SLDPRT]
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2016-02-18 add space invaders carriage
    Alternate E3Dv6 carriage design. Nozzle height is significantly higher
    than the original carriage and my not be compatible without other
    changes. More info at http://www.thingiverse.com/thing:1322641.
    [E3D Extruder v3-0 Bottom Clamp.STL, E3D Extruder v3-0 Top Clamp.STL, E3D Extruder v3-0.STEP]
2016-02-20 Volcano Spacer
    Spacer to place between duct and carriage of Walter's mini Space
    Invaders Carriage for the E3Dv6 Volcano.
    [Walters Mini Extruder Volcano Spacer v1.f3d, Walters Mini Extruder Volcano Spacer v1.iges, Walters Mini Extruder Volcano Spacer v1.step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]
2016-02-21 AIO Duct/Spacer
    All in one duct spacer combination to convert Walter's Space Invaders
    Carriage for use with the E3Dv6 Volcano.
    [Walters Mini Space Invaders Volcano Duct v1.f3d, Walters Mini Space Invaders Volcano Duct v1.iges, Walters Mini Space Invaders Volcano Duct v1.step]
2016-03-23 Made a correction of the lineage of these printers to include Brad Hill's Tslot Tantillus
    I feel bad that I incorrectly listed Tim's Ingentis coming directly after Sublimes Tantillus. In fact it was GoopyPlastic (AKA Brad Hill who later designed the great little RP SLA printer) who designed the Tslot Tantillus from which Tim designed his Ingentis. I apologize for missing the great work of Brad in my summary up until now.
2016-06-20 Mounts and Models for Azteeg X5 Mini V3
    Added mounts, controller models, and more for the Azteeg X5 Mini V3
    printer controller. Side panel will need to be modified still to line up
    with the ports on the stacked version of the controller and raspberry
    Pi3 electronics package.
    [2x1 Mhdr.sldprt, 2x2 Mhdr.sldprt, 2x3 Mhdr.sldprt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]
2016-11-06 Added model files for the ball screw and a print
    Added model files for the ball screw and a print
    [Ballscrew to Replace Misumi in Erics Eustathios 1.5.sldprt, Eustathios Ball Screw Upgrade.SLDDRW, Eustathios Ball Screw.SLDASM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]
2016-11-06 Moved the ball screw files into the correct directory
    Moved the ball screw files into the correct directory
    [Ballscrew to Replace Misumi in Erics Eustathios 1.5.sldprt, Eustathios Ball Screw Upgrade.SLDDRW, Eustathios Ball Screw.SLDASM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]
2016-11-06 fixed bad web upload which added wierd directory
    fixed bad web upload which added wierd directory
    [Ballscrew to Replace Misumi in Erics Eustathios 1.5.sldprt, Eustathios Ball Screw Upgrade.SLDDRW, Eustathios Ball Screw.SLDASM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]
2017-04-14 Eustathios Bondtech BMG Direct Drive Carriage
    Eustathios Bondtech BMG Direct Drive Carriage
    [Carriage_Eustathios_BMG.STL, Eustathios Direct Drive Carriage.x_t, Part Cooling.STL]
2017-11-22 Smoothieboard config file
    Config file for Eustathios V2 running on original smoothieboard and latest edge firmware (22.11.2017)
    Setup used:
    - I use walter's carriage. hotend fan is always powered so no switch config
    Parts fans are on 2.4 with PWM
    - no bed probe, a well levelled bed is all you need ;)
    - hotend on 2.7, sensor 0.23
    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
    [Smoothieboard config.txt]
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2018-02-03 Dennis P Additions and Re-Mixes
    Addions of helper parrs and remixes of originals to include TR8X8 Z screws, brass heatserts in places, etc....
    [Cable Ring Low.stl, Cable Ring.stl, Z-Bed_Support_Hsiao.dxf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]
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2018-02-08 Relocated Z Motor Mount
    Relocated Z Motor Mount to facilitate a shorter drive belt.
    [Z-Motor_Bracket.stl]
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2018-02-20 Updated BOM with some changes
    Made some BOM changes and corrections based on user notes
    [Eustathios Spider V2 BOM (updated 02-20-18).xlsx]
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2019-11-08 Added STL and Solidworks parts for compact Carriage with BL Touch
    Added STL and Solidworks files for Compact Carriage with BLTouch.
    I also included Step and X_T for people to import into other CAD packages.
    [4020Blower_R3.SLDPRT, 430200801.SLDPRT, 430250808.SLDPRT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]
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2020-06-16 Add Missing File
    Add Missing File
    [molex_microfit_female_containment.SLDPRT]
